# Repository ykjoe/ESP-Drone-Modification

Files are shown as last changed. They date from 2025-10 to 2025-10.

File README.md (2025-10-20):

# ESP-Drone

image_tooltip
<br>

<br>

For a full tutorial check out our [ESP32 Drone Article](https://circuitdigest.com/microcontroller-projects/DIY-wifi-controlled-drone).
For working video:  [How to build an ESP32 Drone](https://youtu.be/uzZjk0TQKtU).

Drones have rapidly evolved from niche hobbies to versatile tools with a wide range of applications, from photography to agriculture or even for defense and military purposes. Depending on the application, features and payload capacity their price will vary from pocket changes to a few million. Even though the basic principle behind these drones may appear simple, there is a lot of technology and computation that goes behind it for proper operations and a desired result from these drones. For example, maintaining stability while in the air requires precision sensors such as a Gyroscope and proper processing of reading taken with it. In this project we are going to make such a drone which can be easily controlled using our phones.
This DIY drone is small in size and can be built using easily available components such as ESP32 modules, MPU6050 IMU, coreless motors and plastic propellers.

<br>**For anyone who is trying to flash the firmware using ESP32 Flash Download Tool, here are the file offsets for each binary**
<br>**0x1000 bootloader.bin**
<br>**0x8000 partition-table.bin**
<br>**0x10000 ESPDrone.bin**
<br>
[Note: As this projects are very simple we are only providing the code, schemaitic, and a few essential images if you want to get the images or code explanations do check out the Circuit Digest website.
<br>
<br>

Copy from: https://github.com/Circuit-Digest/ESP-Drone.git

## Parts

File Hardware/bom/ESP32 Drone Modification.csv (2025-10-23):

Reference | Value | Datasheet | Footprint | Qty | DNP | Manufacturer_Name
C1,C4,C5 | 10uF | ~ | Capacitor_SMD:C_0603_1608Metric | 3
C2 | 470pF | ~ | Capacitor_SMD:C_0603_1608Metric | 1
C3 | 2.2uF | ~ | Capacitor_SMD:C_0805_2012Metric | 1
C6,C11,C13 | 0.1uf | ~ | Capacitor_SMD:C_0603_1608Metric | 3
C7,C9,C14 | 10uf | ~ | Capacitor_SMD:C_0603_1608Metric | 3
C8,C10,C15,C16,C17,C18 | 1uf | ~ | Capacitor_SMD:C_0603_1608Metric | 6
C12 | 0.1uF | ~ | Capacitor_SMD:C_0603_1608Metric | 1
D1 | SS34 | https://www.vishay.com/docs/88751/ss32.pdf | Diode_SMD:D_SMA | 1 |  | TWGMC/UMW
D2,D3,D4,D5 | 1N4148W | https://www.vishay.com/docs/85748/1n4148w.pdf | Diode_SMD:D_SOD-123 | 4 |  | R+O
IC1 | TP4056 | https://datasheet.lcsc.com/szlcsc/1906261508_Nanjing-Extension-Microelectronics-TP4056-42-ESOP8_C16581.pdf | loc_footprints:SOIC127P600X175-9N | 1 |  | Nanjing Extension Microelectronics
J1 | USB_C_Receptacle_USB2.0 | https://www.usb.org/sites/default/files/documents/usb_type-c.zip | Connector_USB:USB_C_Receptacle_HRO_TYPE-C-31-M-12 | 1 |  | XUNPU
J2,J4,J5,J6 | Conn_01x02_Socket | ~ | Connector_JST:JST_GH_SM02B-GHS-TB_1x02-1MP_P1.25mm_Horizontal | 4 |  | JST
J3 | B2B-PH-SM4-TB(LF)(SN) | https://octopart.com/zh/datasheet/b2b-ph-sm4-tb%28lf%29%28sn%29-jst-248898 | Connector_JST:JST_PH_B2B-PH-SM4-TB_1x02-1MP_P2.00mm_Vertical | 1 |  | JST
J8,J9 | Conn_01x06_Socket | ~ | Connector_PinHeader_2.54mm:PinHeader_1x06_P2.54mm_Vertical | 2
LED1 | POW_LED | ~ | LED_SMD:LED_0603_1608Metric | 1
LED2,LED3 | CHG | ~ | LED_SMD:LED_0603_1608Metric | 2
LED4,LED5,LED6 | LED | ~ | LED_SMD:LED_0603_1608Metric | 3
Q1 | AO3401A | http://www.aosmd.com/pdfs/datasheet/AO3401A.pdf | Package_TO_SOT_SMD:SOT-23 | 1 |  | AOS/UMW
R1 | 470R | ~ | Resistor_SMD:R_0603_1608Metric | 1
R2,U4,U5 | 100K | ~ | Resistor_SMD:R_0603_1608Metric | 3
R3,R4 | 1k3 | ~ | Resistor_SMD:R_0603_1608Metric | 2
R5 | 47.5k | ~ | Resistor_SMD:R_0603_1608Metric | 1
R6 | 22.1k | ~ | Resistor_SMD:R_0603_1608Metric | 1
R7,R10,R11,R12,R14,R18,R19,R20,R21 | 10k | ~ | Resistor_SMD:R_0603_1608Metric | 9
R8,R9 | 1k | ~ | Resistor_SMD:R_0603_1608Metric | 2
R13 | 4.7k | ~ | Resistor_SMD:R_0603_1608Metric | 1
R15,R16,R17 | 1K | ~ | Resistor_SMD:R_0603_1608Metric | 3
R22 | 100k | ~ | Resistor_SMD:R_0603_1608Metric | 1
Rprog1 | 3.3K | ~ | Resistor_SMD:R_0603_1608Metric | 1
SW1 | K3-1280S-F1 | ~ | loc_footprints:slide switch spdt | 1 |  | HRO
T1,T2,T3,T4 | SI2302DS-T1 |  | loc_footprints:SOT95P237X112-3N | 4 |  | Vishay
U3 | MIC5219-3.3YM5 | http://ww1.microchip.com/downloads/en/DeviceDoc/MIC5219-500mA-Peak-Output-LDO-Regulator-DS20006021A.pdf | Package_TO_SOT_SMD:SOT-23-5 | 1 |  | Microchip
U6 | CP2102N-Axx-xQFN28 | https://www.silabs.com/documents/public/data-sheets/cp2102n-datasheet.pdf | Package_DFN_QFN:QFN-28-1EP_5x5mm_P0.5mm_EP3.35x3.35mm | 1 |  | SKYWORKS/SILICON LABS
U7 | DDC114TU-7-F | https://www.diodes.com/assets/Datasheets/DDC_XXXX_U.pdf | Package_TO_SOT_SMD:SOT-363_SC-70-6 | 1 |  | DIODES
U8 | ESP32-WROOM-32 | https://www.espressif.com/sites/default/files/documentation/esp32-wroom-32_datasheet_en.pdf | RF_Module:ESP32-WROOM-32 | 1 |  | ESPRESSIF
U9 | MPU-6050 | https://invensense.tdk.com/products/motion-tracking/6-axis/mpu-6050/ | loc_footprints:MPU6050 | 1 |  | TDK

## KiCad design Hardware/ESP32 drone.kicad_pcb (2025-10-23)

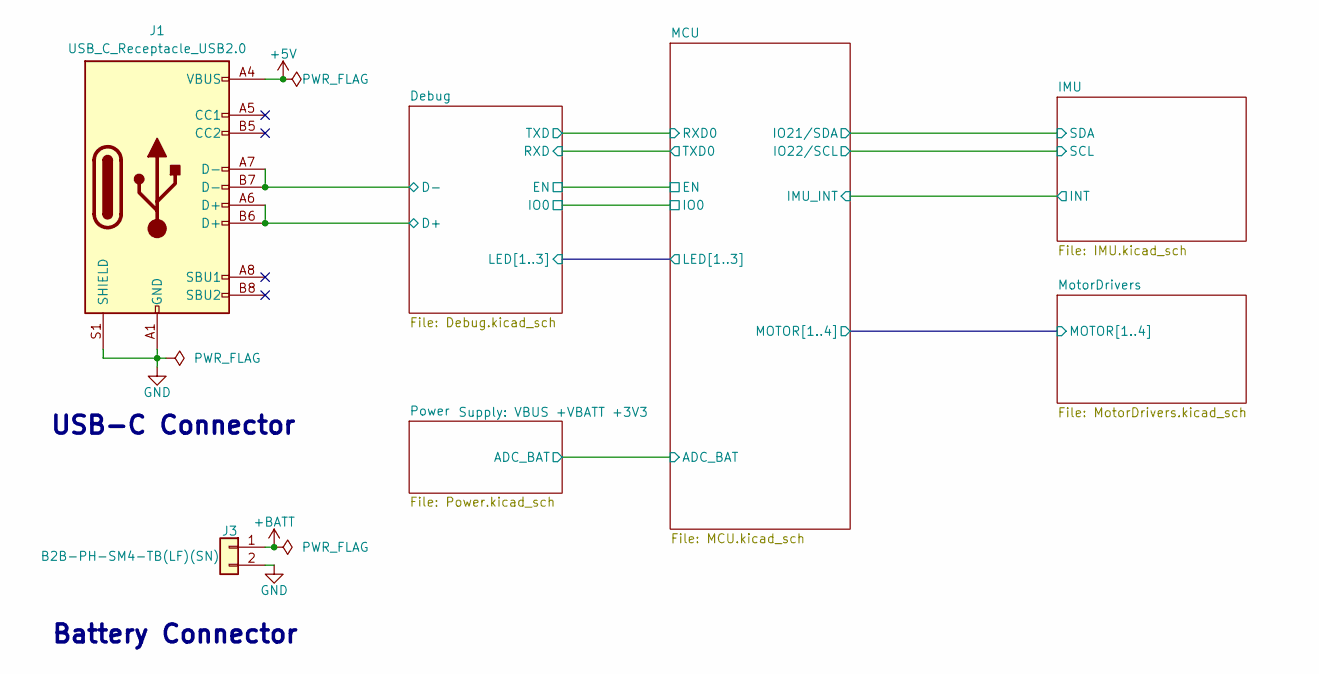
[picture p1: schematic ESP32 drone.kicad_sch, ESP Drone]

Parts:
J1: USB_C_Receptacle_USB2.0; USB_C_Receptacle_HRO_TYPE-C-31-M-12
J3: B2B-PH-SM4-TB(LF)(SN); JST_PH_B2B-PH-SM4-TB_1x02-1MP_P2.00mm_Vertical

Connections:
+5V: J1.A4 (VBUS), J1.A9 (VBUS), J1.B4 (VBUS), J1.B9 (VBUS); also elsewhere on the board
+BATT: J3.1; also elsewhere on the board
/Debug/D+: J1.A6 (D+), J1.B6 (D+); also elsewhere on the board
/Debug/D-: J1.A7 (D-), J1.B7 (D-); also elsewhere on the board
GND: J1.A1 (GND), J1.A12 (GND), J1.B1 (GND), J1.B12 (GND), J1.S1 (SHIELD), J3.2; also elsewhere on the board

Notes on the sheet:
Battery Connector
USB-C Connector

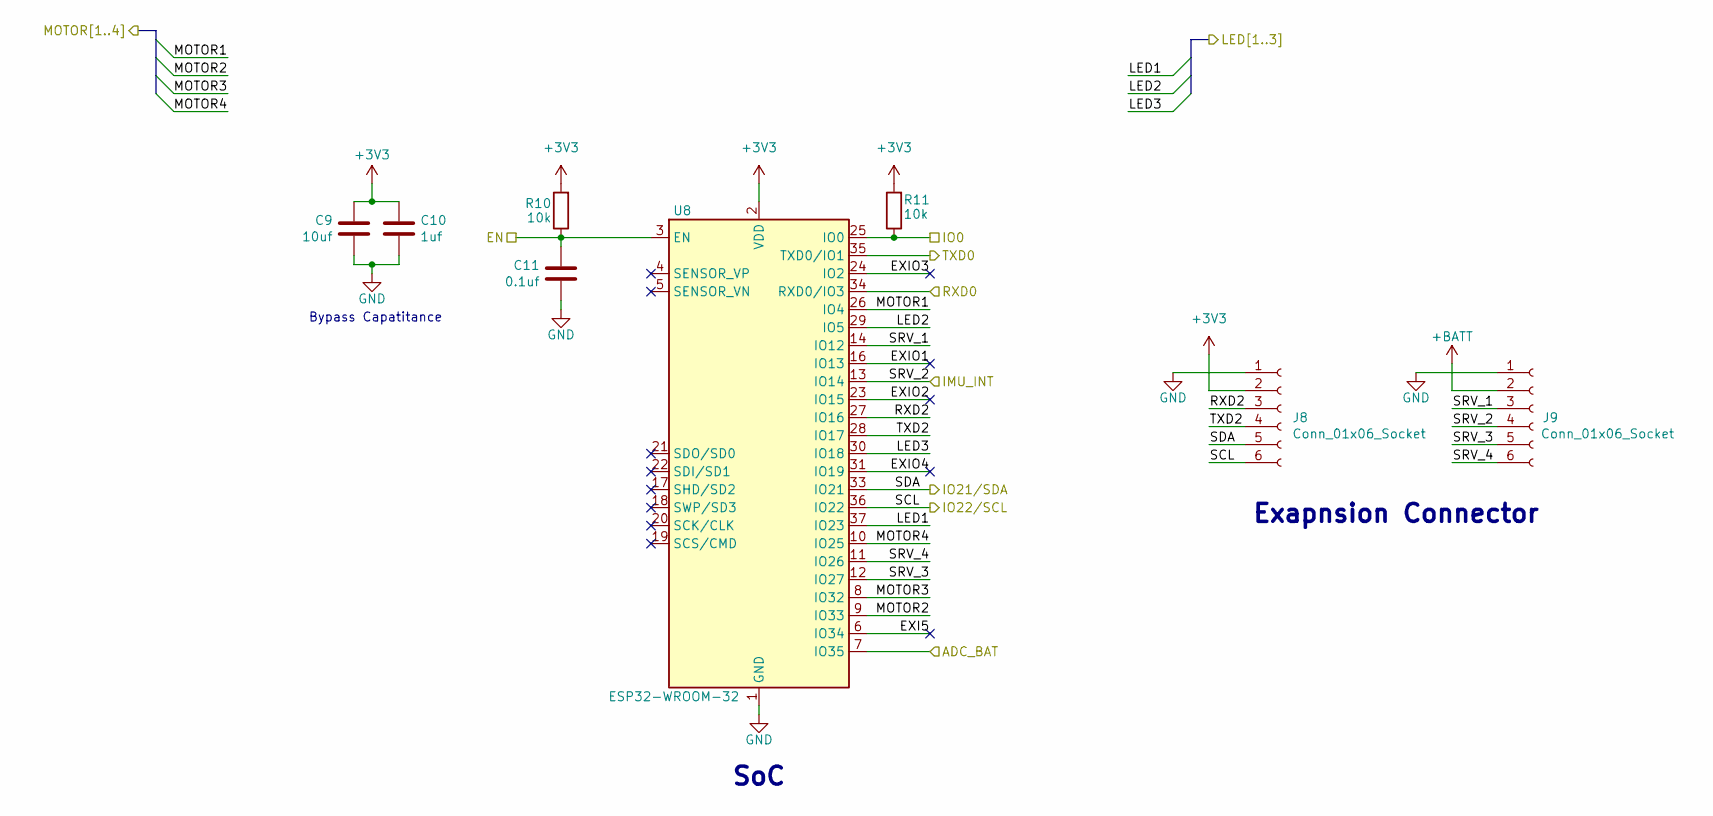
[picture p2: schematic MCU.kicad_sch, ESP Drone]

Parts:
C9: 10uf; C_0603_1608Metric
C10: 1uf; C_0603_1608Metric
C11: 0.1uf; C_0603_1608Metric
J8, J9: Conn_01x06_Socket; PinHeader_1x06_P2.54mm_Vertical
R10, R11: 10k; R_0603_1608Metric
U8: ESP32-WROOM-32

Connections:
+3V3: C9.1, C10.1, J8.2, R10.2, R11.2, U8.2 (VDD); also elsewhere on the board
+BATT: J9.2; also elsewhere on the board
/Debug/EN: C11.1, R10.1, U8.3 (EN); also elsewhere on the board
/Debug/IO0: R11.1, U8.25 (IO0); also elsewhere on the board
/Debug/LED1: U8.37 (IO23); also elsewhere on the board
/Debug/LED2: U8.29 (IO5); also elsewhere on the board
/Debug/LED3: U8.30 (IO18); also elsewhere on the board
/Debug/RXD: U8.35 (TXD0/IO1); also elsewhere on the board
/Debug/TXD: U8.34 (RXD0/IO3); also elsewhere on the board
/MCU/ADC_BAT: U8.7 (IO35); also elsewhere on the board
/MCU/EXI5: U8.6 (IO34)
/MCU/EXIO1: U8.16 (IO13)
/MCU/EXIO2: U8.23 (IO15)
/MCU/EXIO3: U8.24 (IO2)
/MCU/EXIO4: U8.31 (IO19)
/MCU/MOTOR1: U8.26 (IO4); also elsewhere on the board
/MCU/MOTOR2: U8.9 (IO33); also elsewhere on the board
/MCU/MOTOR3: U8.8 (IO32); also elsewhere on the board
/MCU/MOTOR4: U8.10 (IO25); also elsewhere on the board
/MCU/RXD2: J8.3, U8.27 (IO16)
/MCU/SCL: J8.6, U8.36 (IO22); also elsewhere on the board
/MCU/SDA: J8.5, U8.33 (IO21); also elsewhere on the board
/MCU/SRV_1: J9.3, U8.14 (IO12)
/MCU/SRV_2: J9.4, U8.13 (IO14); also elsewhere on the board
/MCU/SRV_3: J9.5, U8.12 (IO27)
/MCU/SRV_4: J9.6, U8.11 (IO26)
/MCU/TXD2: J8.4, U8.28 (IO17)
GND: C9.2, C10.2, C11.2, J8.1, J9.1, U8.1 (GND), U8.15 (GND), U8.38 (GND), U8.39 (GND); also elsewhere on the board

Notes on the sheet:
Exapnsion Connector
Bypass Capatitance
SoC

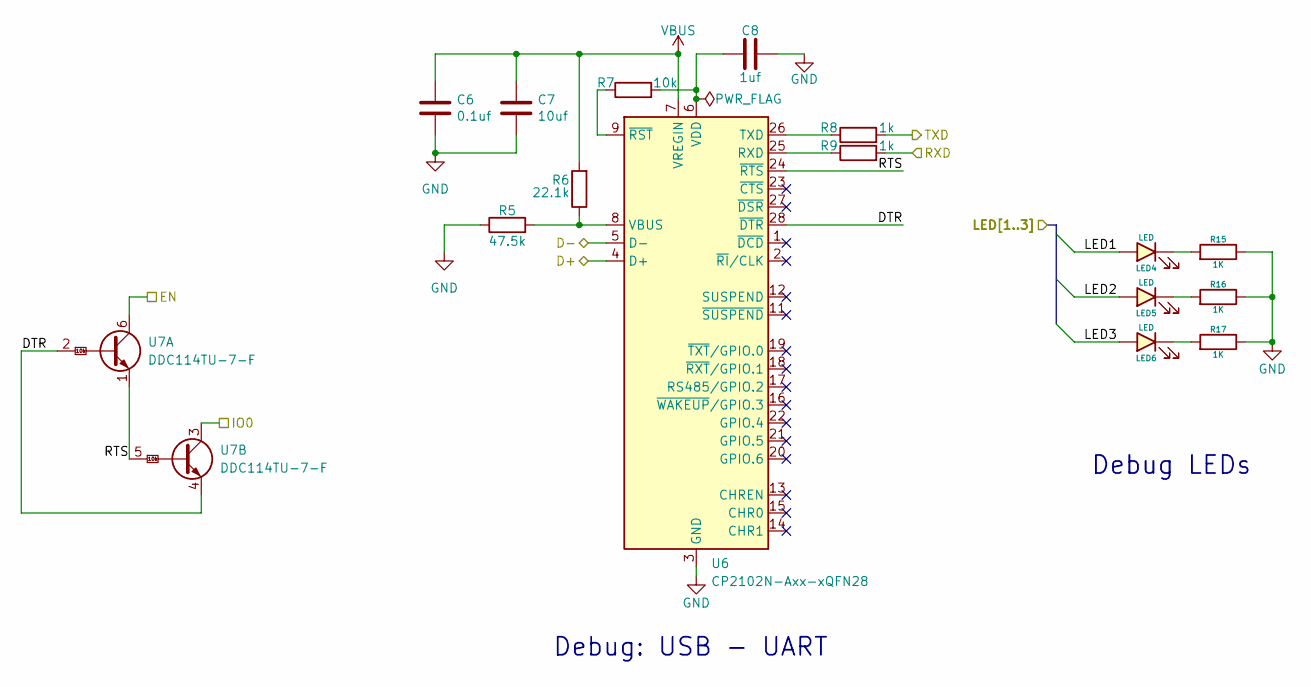
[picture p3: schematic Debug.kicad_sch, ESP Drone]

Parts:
C6: 0.1uf; C_0603_1608Metric
C7: 10uf; C_0603_1608Metric
C8: 1uf; C_0603_1608Metric
LED4, LED5, LED6: LED; LED_0603_1608Metric
R5: 47.5k; R_0603_1608Metric
R6: 22.1k; R_0603_1608Metric
R7: 10k; R_0603_1608Metric
R8, R9: 1k; R_0603_1608Metric
R15, R16, R17: 1K; R_0603_1608Metric
U6: CP2102N-Axx-xQFN28; QFN-28-1EP_5x5mm_P0.5mm_EP3.35x3.35mm
U7: DDC114TU-7-F; SOT-363_SC-70-6

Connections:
/Debug/D+: U6.4 (D+); also elsewhere on the board
/Debug/D-: U6.5 (D-); also elsewhere on the board
/Debug/DTR: U6.28 (~DTR), U7.2 (B1), U7.4 (E2)
/Debug/EN: U7.6 (C1); also elsewhere on the board
/Debug/IO0: U7.3 (C2); also elsewhere on the board
/Debug/LED1: LED4.2 (A); also elsewhere on the board
/Debug/LED2: LED5.2 (A); also elsewhere on the board
/Debug/LED3: LED6.2 (A); also elsewhere on the board
/Debug/RTS: U6.24 (~RTS), U7.1 (E1), U7.5 (B2)
/Debug/RXD: R9.2; also elsewhere on the board
/Debug/TXD: R8.2; also elsewhere on the board
GND: C6.2, C7.2, C8.2, R5.1, R15.1, R16.1, R17.1, U6.3 (GND), U6.29 (GND); also elsewhere on the board
unnamed: LED4.1 (K), R15.2
unnamed: LED5.1 (K), R16.2
unnamed: LED6.1 (K), R17.2
unnamed: R9.1, U6.25 (RXD)
unnamed: R8.1, U6.26 (TXD)
unnamed: R5.2, R6.1, U6.8 (VBUS)
unnamed: C8.1, R7.2, U6.6 (VDD)
unnamed: R7.1, U6.9 (~RST)
VBUS: C6.1, C7.1, R6.2, U6.7 (VREGIN); also elsewhere on the board

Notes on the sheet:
Debug LEDs
Debug: USB - UART

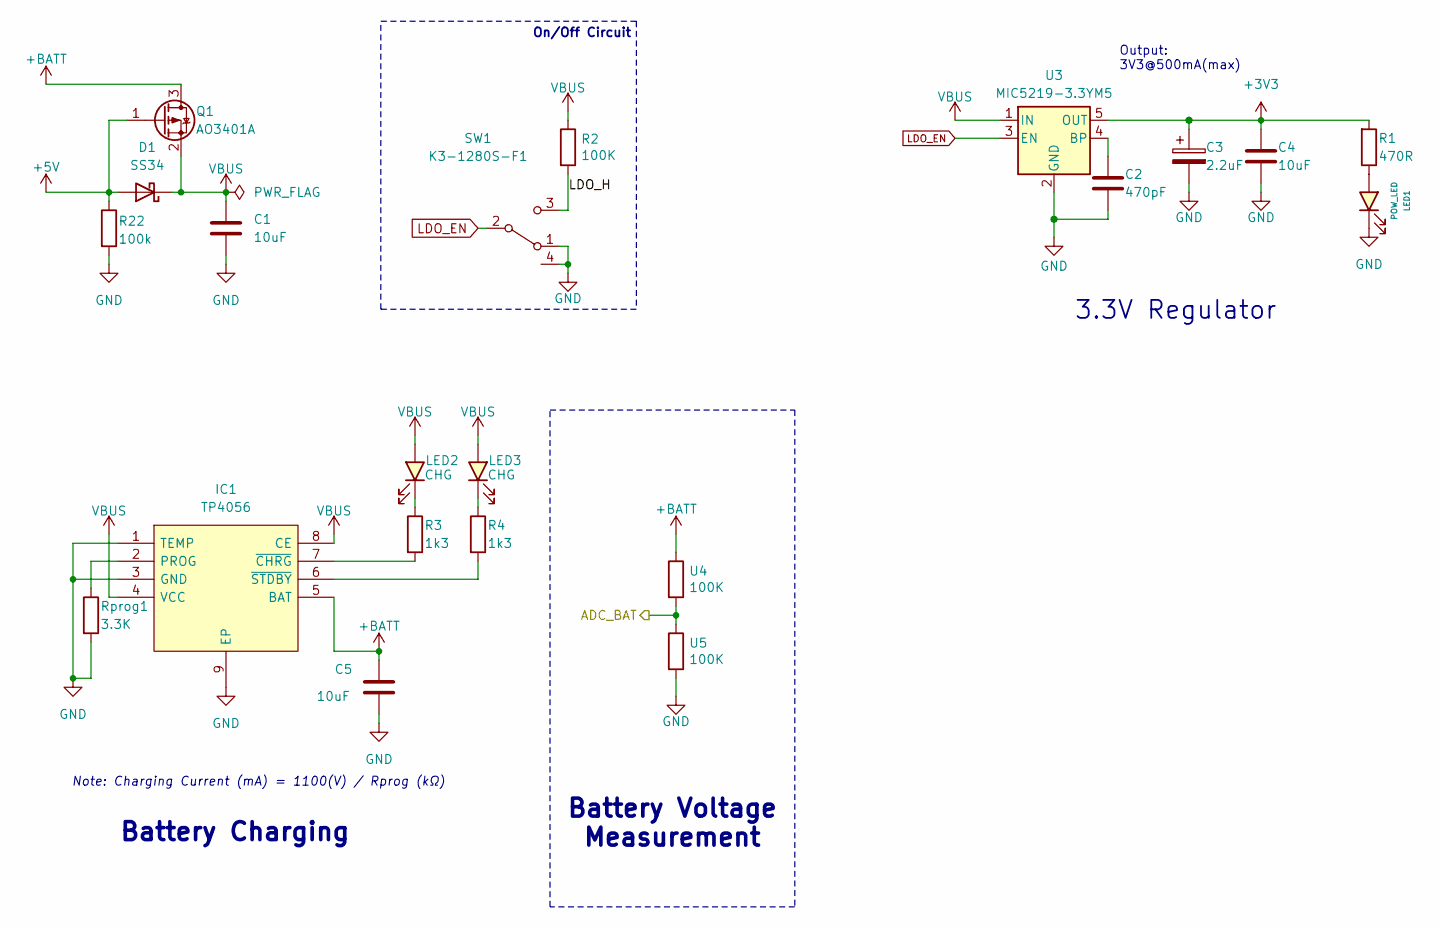
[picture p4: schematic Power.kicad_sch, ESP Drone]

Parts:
C1, C4, C5: 10uF; C_0603_1608Metric
C2: 470pF; C_0603_1608Metric
C3: 2.2uF; C_0805_2012Metric
D1: SS34; D_SMA
IC1: TP4056; SOIC127P600X175-9N; Manufacturer_Part_Number TP4056-42-ESOP8
LED1: POW_LED; LED_0603_1608Metric
LED2, LED3: CHG; LED_0603_1608Metric
Q1: AO3401A; SOT-23
R1: 470R; R_0603_1608Metric
R2: 100K; R_0603_1608Metric
R3, R4: 1k3; R_0603_1608Metric
R22: 100k; R_0603_1608Metric
Rprog1: 3.3K; R_0603_1608Metric
SW1: K3-1280S-F1; slide switch spdt
U3: MIC5219-3.3YM5; SOT-23-5
U4, U5: 100K; R_0603_1608Metric

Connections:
+3V3: C3.1, C4.1, R1.2, U3.5 (OUT); also elsewhere on the board
+5V: D1.2 (A), Q1.1 (G), R22.1; also elsewhere on the board
+BATT: C5.1, IC1.5 (BAT), Q1.3 (D), U4.1; also elsewhere on the board
/MCU/ADC_BAT: U4.2, U5.1; also elsewhere on the board
/Power/LDO_H: R2.2, SW1.3 (C)
GND: C1.2, C2.2, C3.2, C4.2, C5.2, IC1.1 (TEMP), IC1.3 (GND), IC1.9 (EP), LED1.1 (K), R22.2, Rprog1.2, SW1.1 (A), SW1.4, U3.2 (GND), U5.2; also elsewhere on the board
LDO_EN: SW1.2 (B), U3.3 (EN)
unnamed: IC1.2 (PROG), Rprog1.1
unnamed: IC1.7 (~CHRG), R3.2
unnamed: IC1.6 (~STDBY), R4.2
unnamed: LED1.2 (A), R1.1
unnamed: LED2.1 (K), R3.1
unnamed: LED3.1 (K), R4.1
unnamed: C2.1, U3.4 (BP)
VBUS: C1.1, D1.1 (K), IC1.4 (VCC), IC1.8 (CE), LED2.2 (A), LED3.2 (A), Q1.2 (S), R2.1, U3.1 (IN); also elsewhere on the board

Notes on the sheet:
Output: 3V3@500mA(max)
Note: Charging Current (mA) = 1100(V) / Rprog (kΩ)
Battery Voltage Measurement
Battery Charging
On/Off Circuit
3.3V Regulator

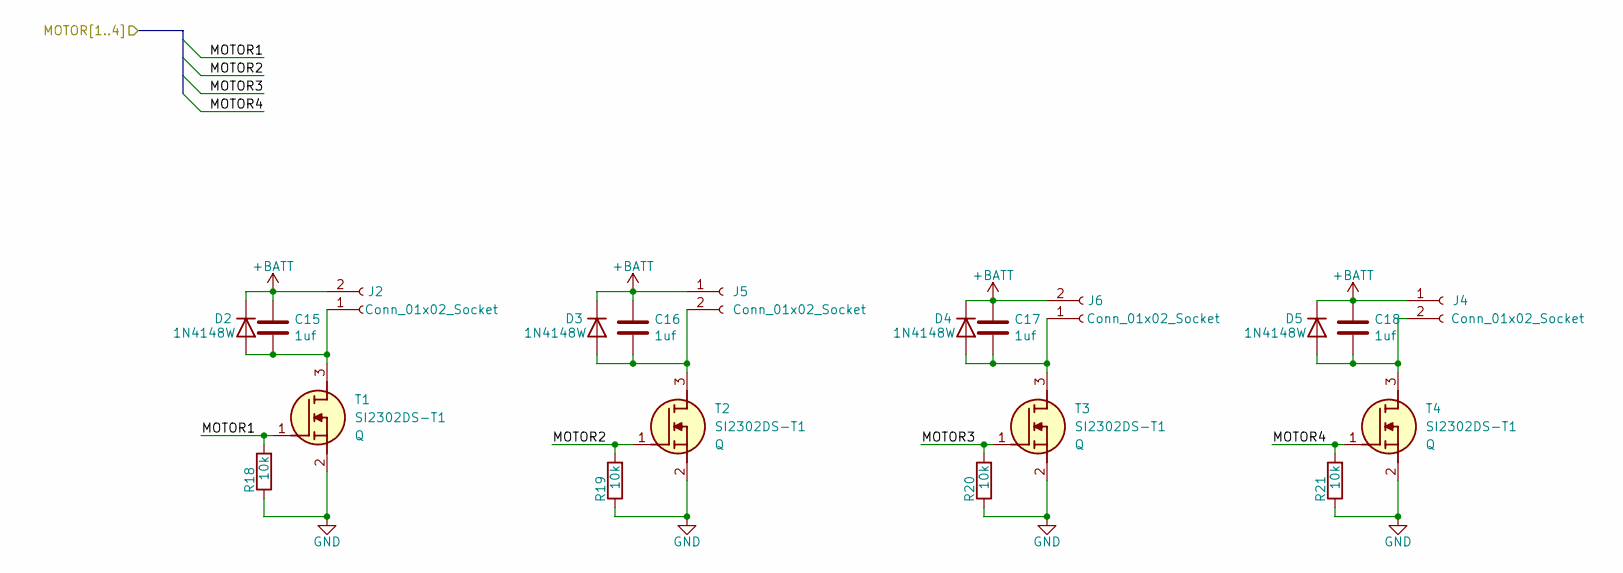
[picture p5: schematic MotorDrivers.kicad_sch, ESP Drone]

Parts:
C15, C16, C17, C18: 1uf; C_0603_1608Metric
D2, D3, D4, D5: 1N4148W; D_SOD-123
J2, J4, J5, J6: Conn_01x02_Socket; JST_GH_SM02B-GHS-TB_1x02-1MP_P1.25mm_Horizontal
R18, R19, R20, R21: 10k; R_0603_1608Metric
T1, T2, T3, T4: SI2302DS-T1; SOT95P237X112-3N; Mouser Part Number 781-SI2302DS

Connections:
+BATT: C15.1, C16.1, C17.1, C18.1, D2.1 (K), D3.1 (K), D4.1 (K), D5.1 (K), J2.2, J4.1, J5.1, J6.2; also elsewhere on the board
/MCU/MOTOR1: R18.2, T1.1 (G); also elsewhere on the board
/MCU/MOTOR2: R19.2, T2.1 (G); also elsewhere on the board
/MCU/MOTOR3: R20.2, T3.1 (G); also elsewhere on the board
/MCU/MOTOR4: R21.2, T4.1 (G); also elsewhere on the board
GND: R18.1, R19.1, R20.1, R21.1, T1.2 (S), T2.2 (S), T3.2 (S), T4.2 (S); also elsewhere on the board
unnamed: C15.2, D2.2 (A), J2.1, T1.3 (D)
unnamed: C16.2, D3.2 (A), J5.2, T2.3 (D)
unnamed: C17.2, D4.2 (A), J6.1, T3.3 (D)
unnamed: C18.2, D5.2 (A), J4.2, T4.3 (D)

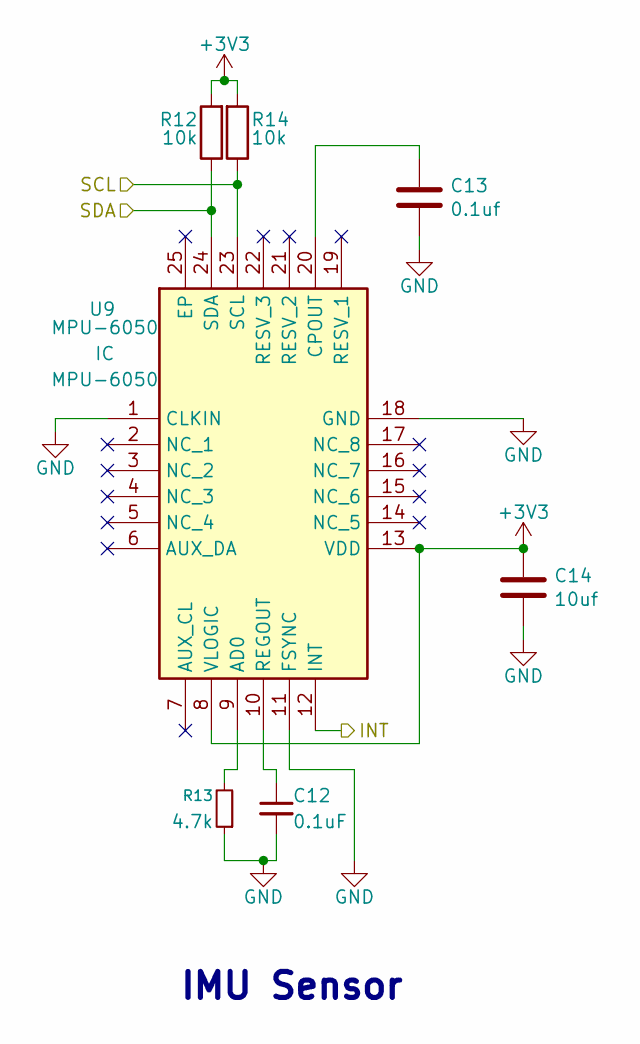
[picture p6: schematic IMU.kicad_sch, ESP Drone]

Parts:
C12: 0.1uF; C_0603_1608Metric
C13: 0.1uf; C_0603_1608Metric
C14: 10uf; C_0603_1608Metric
R12, R14: 10k; R_0603_1608Metric
R13: 4.7k; R_0603_1608Metric
U9: MPU-6050; MPU6050; Mouser Part Number 410-MPU-6050

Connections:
+3V3: C14.1, R12.2, R14.2, U9.8 (VLOGIC), U9.13 (VDD); also elsewhere on the board
/MCU/SCL: R14.1, U9.23 (SCL); also elsewhere on the board
/MCU/SDA: R12.1, U9.24 (SDA); also elsewhere on the board
/MCU/SRV_2: U9.12 (INT); also elsewhere on the board
GND: C12.2, C13.2, C14.2, R13.1, U9.1 (CLKIN), U9.11 (FSYNC), U9.18 (GND); also elsewhere on the board
unnamed: R13.2, U9.9 (AD0)
unnamed: C13.1, U9.20 (CPOUT)
unnamed: C12.1, U9.10 (REGOUT)

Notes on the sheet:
IMU Sensor

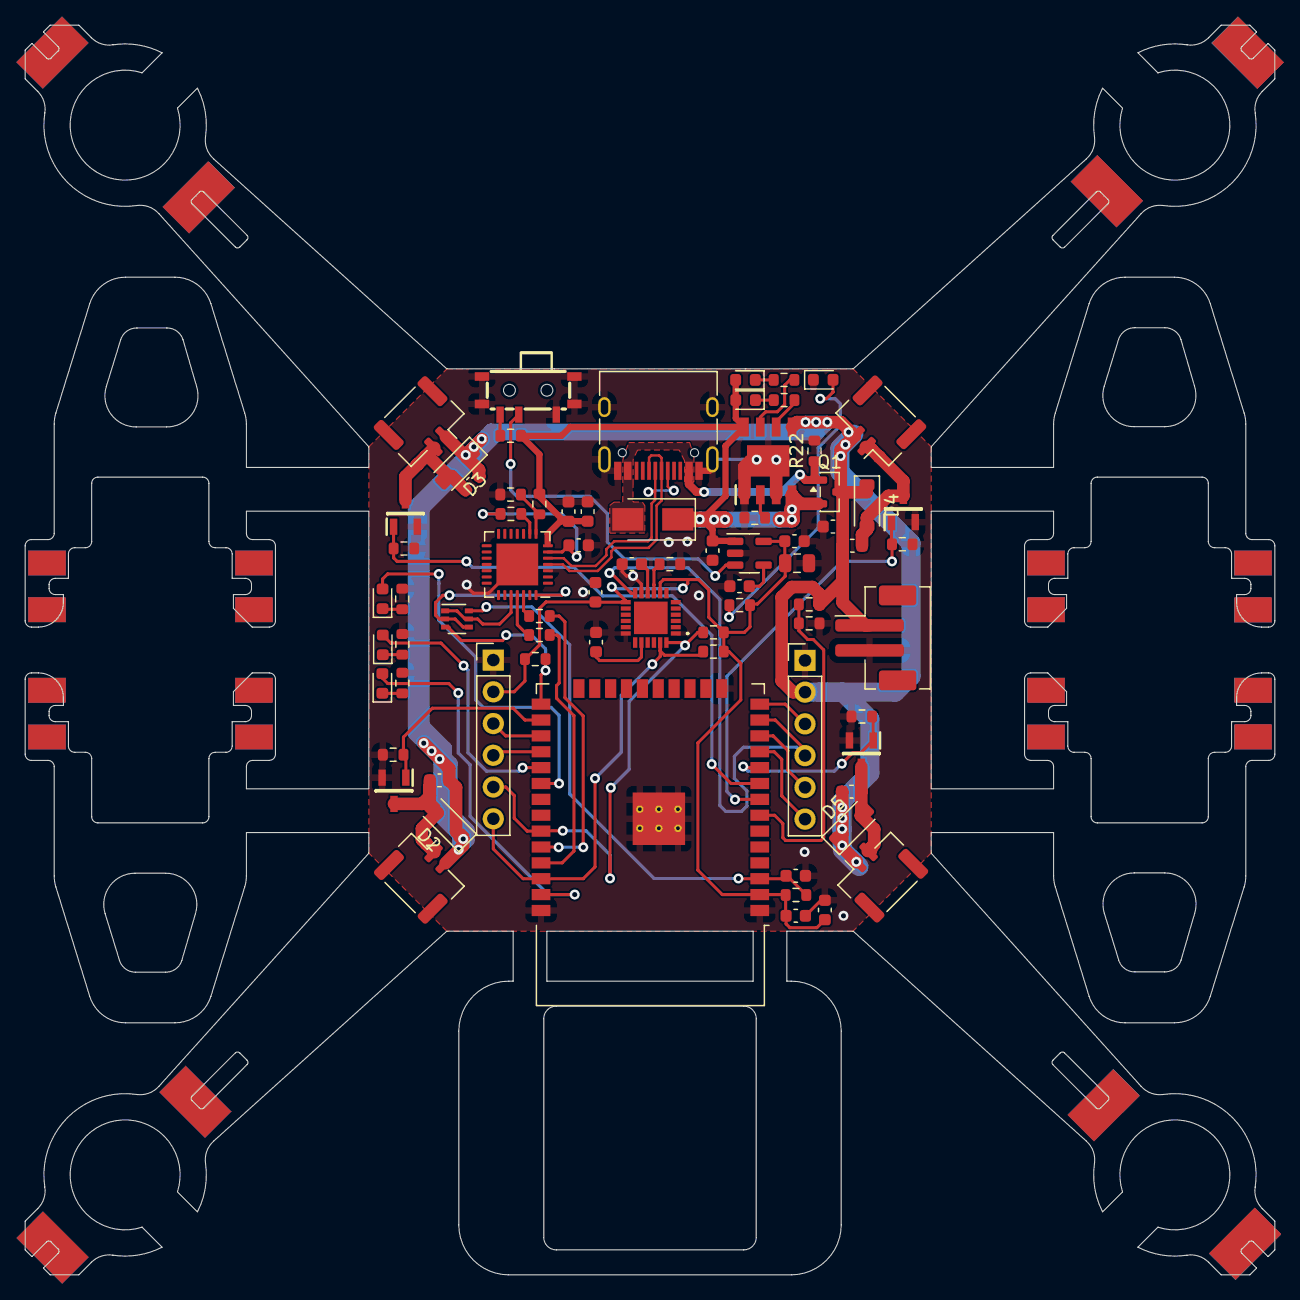
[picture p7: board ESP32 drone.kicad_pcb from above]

Board: 2 copper layers, 100.0 x 100.0 mm, 74 parts (0 on the bottom side), 53 nets.

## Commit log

2025-10-20 Create repo from Circuit-Digest/ESP-Drone
    [ESP32 drone.kicad_pcb, ESP32 drone.kicad_sch, bom.csv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]
2025-10-23 Organize drawings and BOM
    [Debug.kicad_sch, ESP32 Drone Modification.csv, ESP32 drone.kicad_pcb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]
